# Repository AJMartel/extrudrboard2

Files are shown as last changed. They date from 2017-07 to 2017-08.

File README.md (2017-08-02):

# Extrudrboard2
Proposed revision of [Printrbot] [Extrudrboard] for
multi-color/multimaterial printing

Thing tracker at
https://cscott.github.io/thing-tracker/#/thing/737eb982-b77f-43e0-ae38-4fc30f3e3170

## Description

The latest revision of the [Printrboard] (REV F6) is mildly incompatible
with the original [Extrudrboard],
since the HOTEND A signal used by the Extrudrboard was disconnected
and used to provide an extruder fan output.

Also, multimaterial printing doesn't actually need all of the extra
hotend and thermistor inputs.

This repo contains a proposed "Extrudrboard2" which is compatible with
Printrboard REV F6 and provides up to four additional stepper outputs,
used for multimaterial bowden extruders.  The original Printrboard
extruder stepper is used for the direct drive just before the hotend,
and these additional Extrudrboard outputs are multiplexed and used for
the individual filament options.

As a bonus, I've thrown in a FAN2 output for owners of REV F5 and
earlier Printrboards, which adds an extruder fan output which works
identically to that on the REV F6 Printrboard.

The multiplexing scheme here is inspired by the "[Super Switch]" of
Prusa, and in fact basically the same [Marlin] code (`MK2_MULTIPLEXER`)
can be used.  One wrinkle is that the Printrboard extruder output
(we'll call it E0) wants to be a [Gear Head Extruder] with 127
steps/mm, while the individual bowden drivers (E1-E4, driven by the
Extrudrboard2) may be the lower cost 96 steps/mm [Alu Extruder]s --
or even the short-lived injection-molded plastic extruder.  So some
software cleverness is needed to allow multiplexing different
extruders with potentially different steps/mm rates.

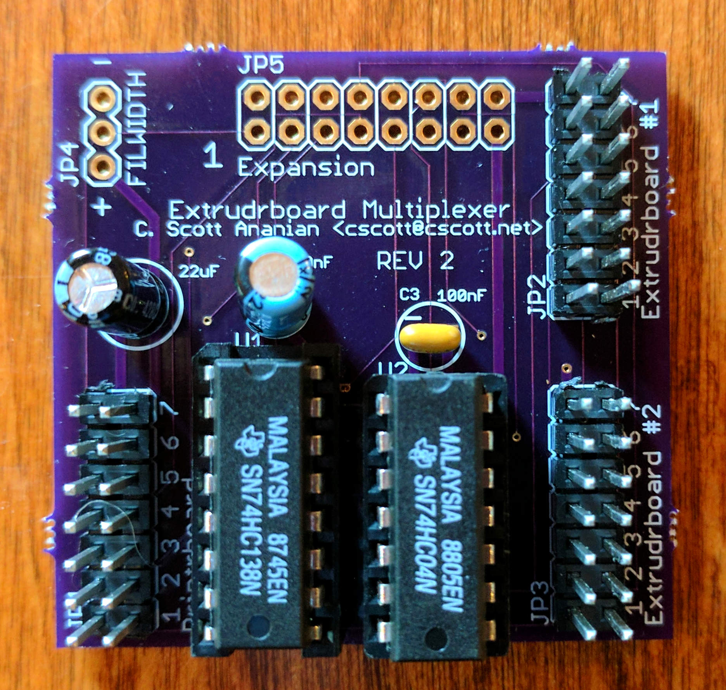
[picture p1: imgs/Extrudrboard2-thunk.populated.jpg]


There are two versions of the board here.  The [`Extrudrboard2-thunk.sch`]
files are an initial
prototype that allows you to connect two original Extrudrboards to the
Printrboard using the new multiplexing signal scheme.  It uses some
random logic ICs for the multiplexer that I just happened to have in
my toolbox.  There was a three-unit minimum order, so I've got a couple extra.  You
could also order this from [OSH Park] as shared project
[wLrvnUeh](https://oshpark.com/shared_projects/wLrvnUeh) -- warning,
boards are not yet tested!

If Printrbot decided to actually adopt this "project" as a "product",
they'd want something more like [`Extrudrboard2.sch`], which integrates the
four stepper drivers from the two old extrudrboards into a single new
board.  I actually reused as much as possible of the original
Extrudrboard schematic, components, and component packages, so this
should be highly compatible with whatever manufacturing process
Printrbot had for the original Extrudrboard.

<br clear="both" />

## Instructions

### Choose your build

If you have existing [Extrudrboard]s you wish to upgrade to the new
Extrudrboard2 functionality, use [`Extrudrboard2-thunk.sch`] with 1 or
2 original Extrudrboards connected.  If you are making new boards from
scratch, use [`Extrudrboard2.sch`].

### Assembling `Extrudrboard2-thunk`



Populating the PCB is straight-forward.  Three 7x2 0.1" male headers get
soldered in for "Printrboard", "Extrudrboard #1" and "Extrudrboard #2".
Add three bypass caps.  Values are somewhat flexible, but I used one 22uF
(primarily to decouple `FILWIDTH`) and two 0.1uF caps (to decouple the
logic ICs).  Solder in the 74HC138 and 74HC04; use DIP sockets if you like.
Note that the 74HC238 is actually a better fit here, but I just happened
to have a '138 in my toolbox so I added an inverter chip to make it work.
Likewise, you should feel free to use the LS or other variant of the logic
chips if you prefer: we're running on 5V and low speed, so any version
will do.

<br clear="both" />

### Wiring `Extrudrboard2-thunk`

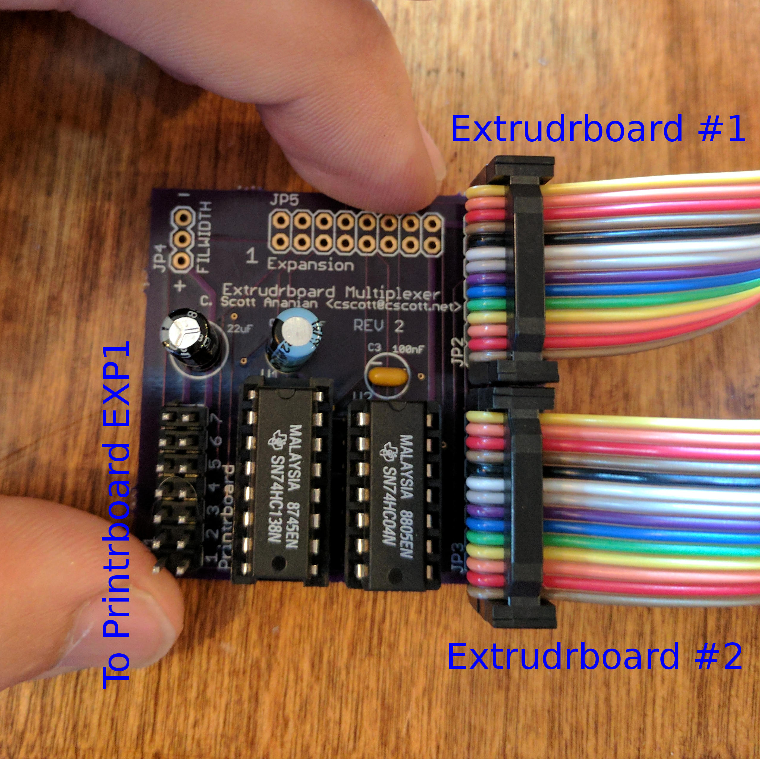
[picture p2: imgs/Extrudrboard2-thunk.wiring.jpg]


Use three 2x7 header cables to connect the Printrboard and two Extrudrboards
as indicated.  The tricky part is keeping pin 1 on the cables oriented
correctly, especially as neither the Printrboard nor the Extrudrboards clearly
mark pin 1.

<br clear="both" />
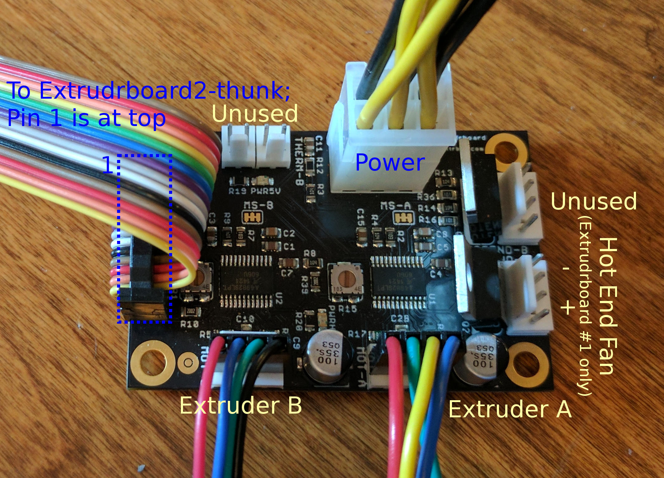
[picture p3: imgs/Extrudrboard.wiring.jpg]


You can connect a hotend fan to the HOTEND A output of Extrudrboard #1.
Pins 1 and 2 are shorted together, as are pins 3 and 4.  You probably
want to use a 1x2 female header on the center two pins.  I've marked
the polarity.

<br clear="both" />

### Additional features of `Extrudrboard2-thunk`

The `FILWIDTH` header is intended to support the Objects with Intelligence
[Filament Width Sensor](http://objectswithintelligence.weebly.com/store.html)
([thing:454584](https://www.thingiverse.com/thing:454584)), at the default
pin assignment used in upstream Marlin.  This is experimental: my
[multimaterial merge project](https://github.com/cscott/3d-multimaterial)
using the Extrudrboard2 doesn't have a place for this, and at the moment
I believe that minimizing distance between the merge and the gear head
drive is essential, so if I wanted to use it I'd likely have to significantly
re-engineer the filament width sensor to minimize the distance it would
add to the unsupported filament path.

The `EXPANSION` header brings all of the unused signals from both the
Printrboard EXP1 connector and the two Extrudrboard connectors into a
convenient place.  The 3 of the 4 HOTEND MOSFETs from the Extrudrboards
are unused (one is connected as an extruder fan output); it should be
convenient to use this header to wire them up to an unused signal from
EXP1 in order to drive some auxiliary load: extra lights, heaters, etc.

### Assembling `Extrudrboard2`

TBD...

### Wiring `Extrudrboard2`

TBD...

## Related

* [Forum discussion for this project](http://forum.monstercafe.net/topic5.html)
* [Multimaterial project](https://github.com/cscott/3d-multimaterial)
* [Repo for original Printrboard/Extruderboard](https://github.com/Printrbot/printrboard)

## License

These designs are released under the
[Creative Commons Attribution Share Alike 3.0] license, like the
original [Extrudrboard](https://github.com/Printrbot/printrboard#printrboard).

[Printrbot]: http://printrbot.com
[Printrboard]: http://reprap.org/wiki/Printrboard
[Extrudrboard]: http://reprap.org/wiki/Adding_more_extruders#RAMPS_using_ExtrudrBoard
[Marlin]: http://www.marlinfw.org/
[Super Switch]: https://github.com/prusa3d/Original-Prusa-i3/issues/29
[Gear Head Extruder]: https://printrbot.com/shop/gear-head-extruder-v2/
[Alu Extruder]: https://printrbot.com/shop/printrbot-alu-extruder-v2/
[`Extrudrboard2.sch`]: ./Extrudrboard2.sch.pdf
[`Extrudrboard2-thunk.sch`]: ./Extrudrboard2-thunk.sch.pdf
[OSH Park]: https://oshpark.com
[Creative Commons Attribution Share Alike 3.0]: https://spdx.org/licenses/CC-BY-SA-3.0.html

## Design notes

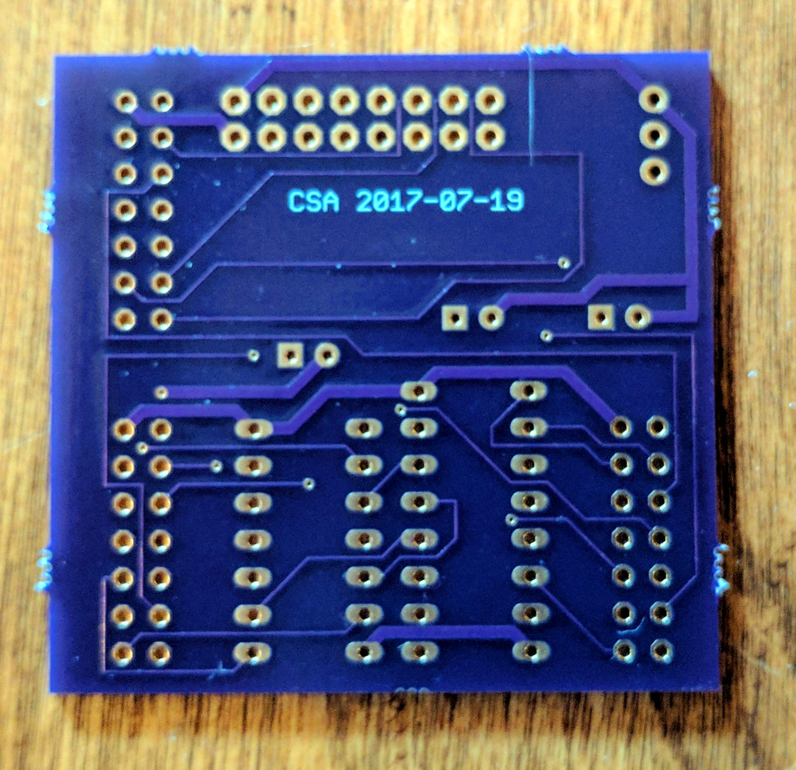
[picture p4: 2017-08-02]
imgs/Extrudrboard2-thunk.brd-back.jpg

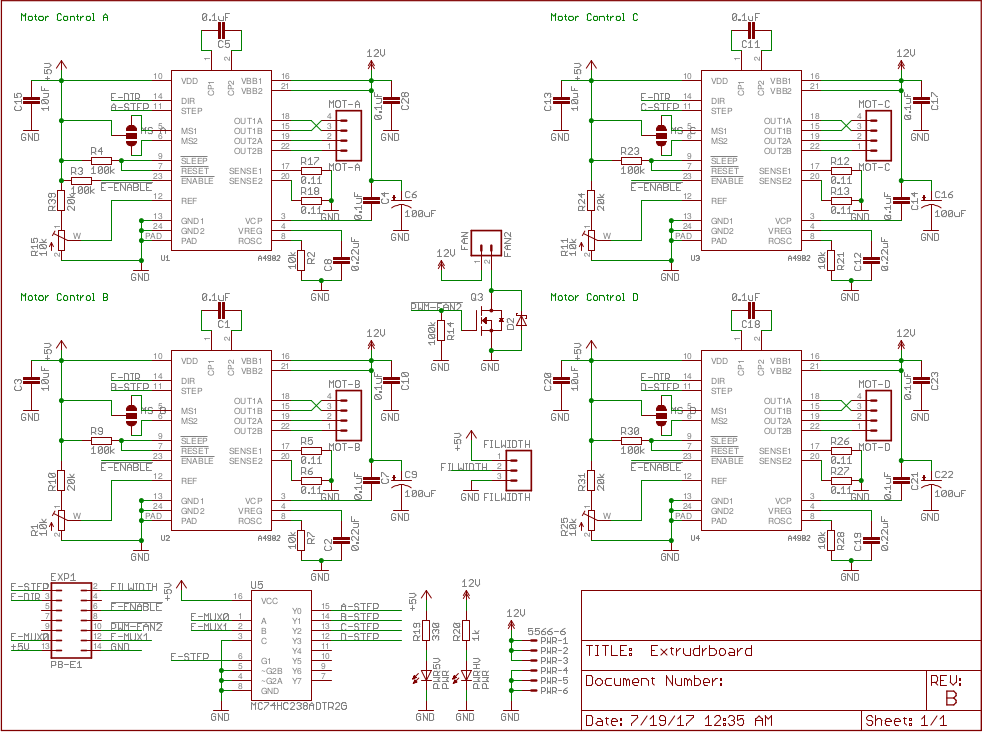
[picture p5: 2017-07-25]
imgs/Extrudrboard2.sch.png

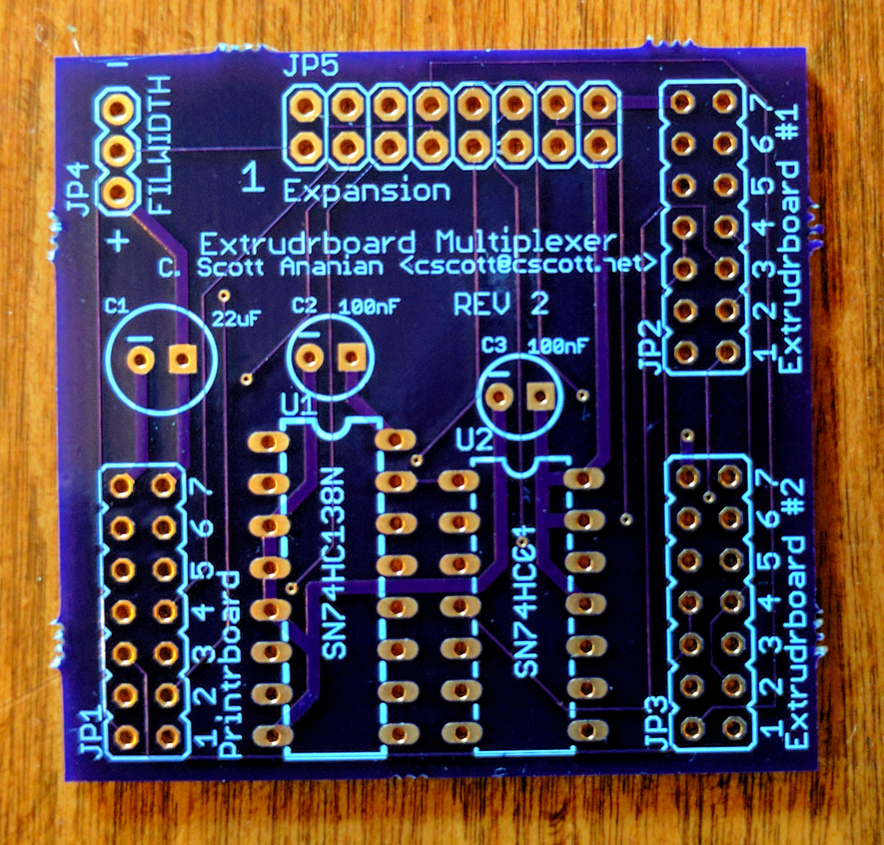
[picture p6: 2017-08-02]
imgs/Extrudrboard2-thunk.brd-front.jpg

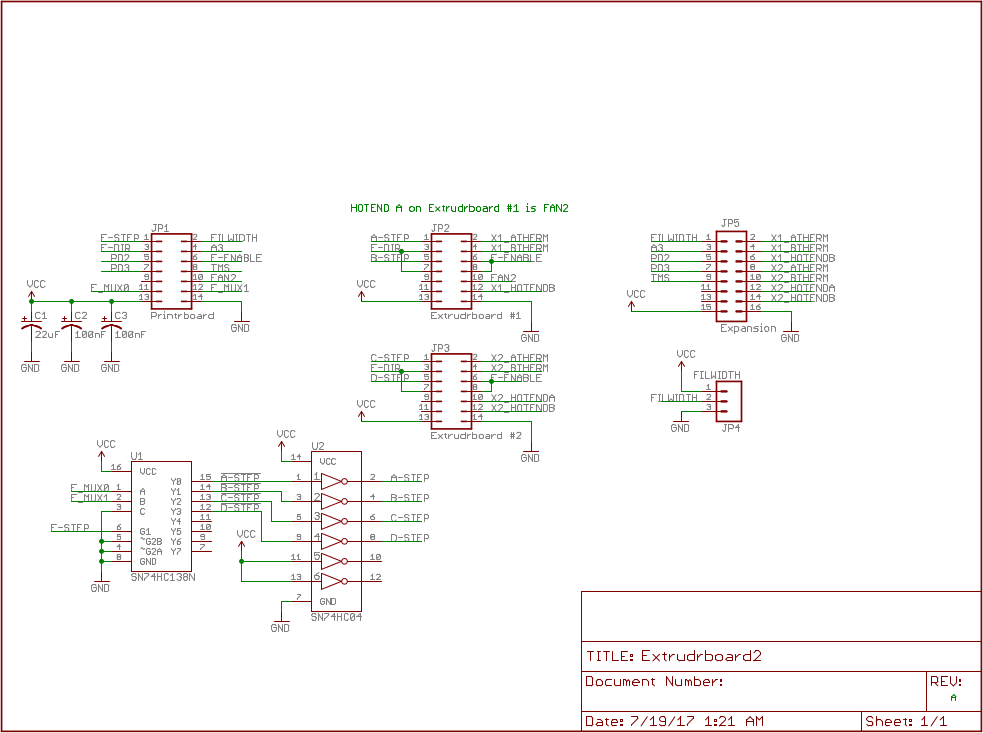
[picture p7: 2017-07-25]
imgs/Extrudrboard2-thunk.sch.png

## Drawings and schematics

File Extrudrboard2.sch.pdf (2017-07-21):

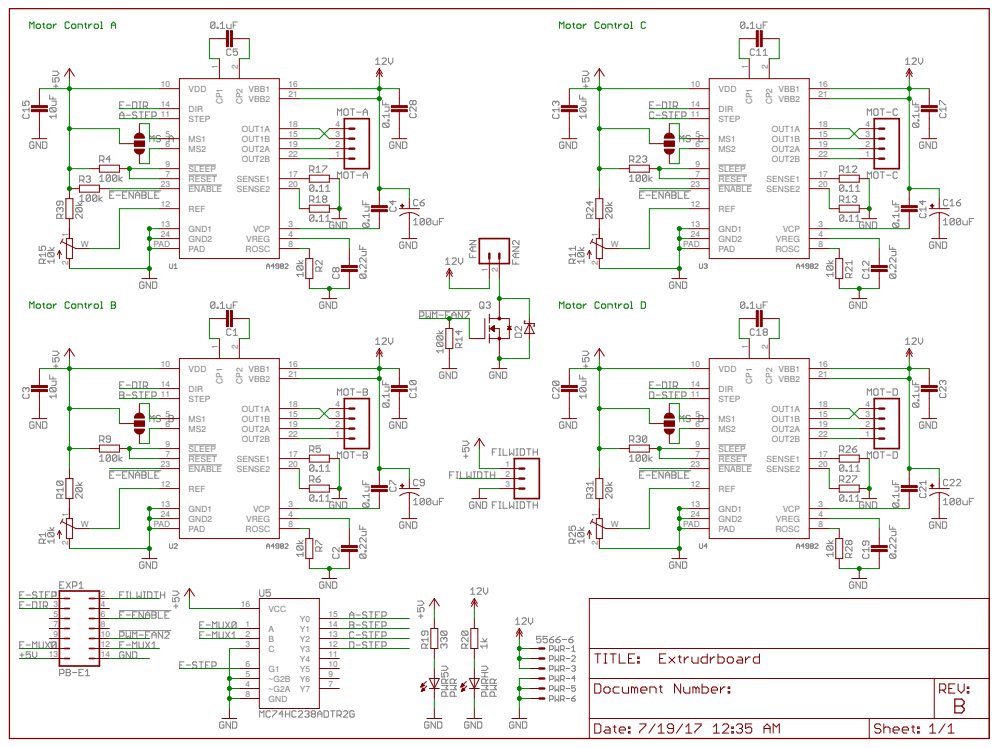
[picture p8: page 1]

2 1 W CP1 1 CP2 2 ROSC 8 VBB2 21 VDD 10 VBB1 16 OUT1A 18 OUT1B 15 OUT2A 19 OUT2B 22 SENSE1 17 SENSE2 20 VREG 4 GND1 13 REF 12 ENABLE 23 MS1 5 RESET 7 STEP 11 DIR 14 VCP 3 SLEEP 9 GND2 24 PAD PAD MS2 6 1234 2 1 W CP1 1 CP2 2 ROSC 8 VBB2 21 VDD 10 VBB1 16 OUT1A 18 OUT1B 15 OUT2A 19 OUT2B 22 SENSE1 17 SENSE2 20 VREG 4 GND1 13 REF 12 ENABLE 23 MS1 5 RESET 7 STEP 11 DIR 14 VCP 3 SLEEP 9 GND2 24 PAD PAD MS2 6 1234 1 2 3 4 5 6 7 8 9 10 11 12 13 14 2 1 W CP1 1 CP2 2 ROSC 8 VBB2 21 VDD 10 VBB1 16 OUT1A 18 OUT1B 15 OUT2A 19 OUT2B 22 SENSE1 17 SENSE2 20 VREG 4 GND1 13 REF 12 ENABLE 23 MS1 5 RESET 7 STEP 11 DIR 14 VCP 3 SLEEP 9 GND2 24 PAD PAD MS2 6 1234 2 1 W CP1 1 CP2 2 ROSC 8 VBB2 21 VDD 10 VBB1 16 OUT1A 18 OUT1B 15 OUT2A 19 OUT2B 22 SENSE1 17 SENSE2 20 VREG 4 GND1 13 REF 12 ENABLE 23 MS1 5 RESET 7 STEP 11 DIR 14 VCP 3 SLEEP 9 GND2 24 PAD PAD MS2 6 1234 VCC 16 A 1 B 2 C 3 G1 6 ~G2B 5 ~G2A 4 GND 8 Y7 7 Y6 9 Y5 10 Y4 11 Y3 12 Y2 13 Y1 14 Y0 15 12 123

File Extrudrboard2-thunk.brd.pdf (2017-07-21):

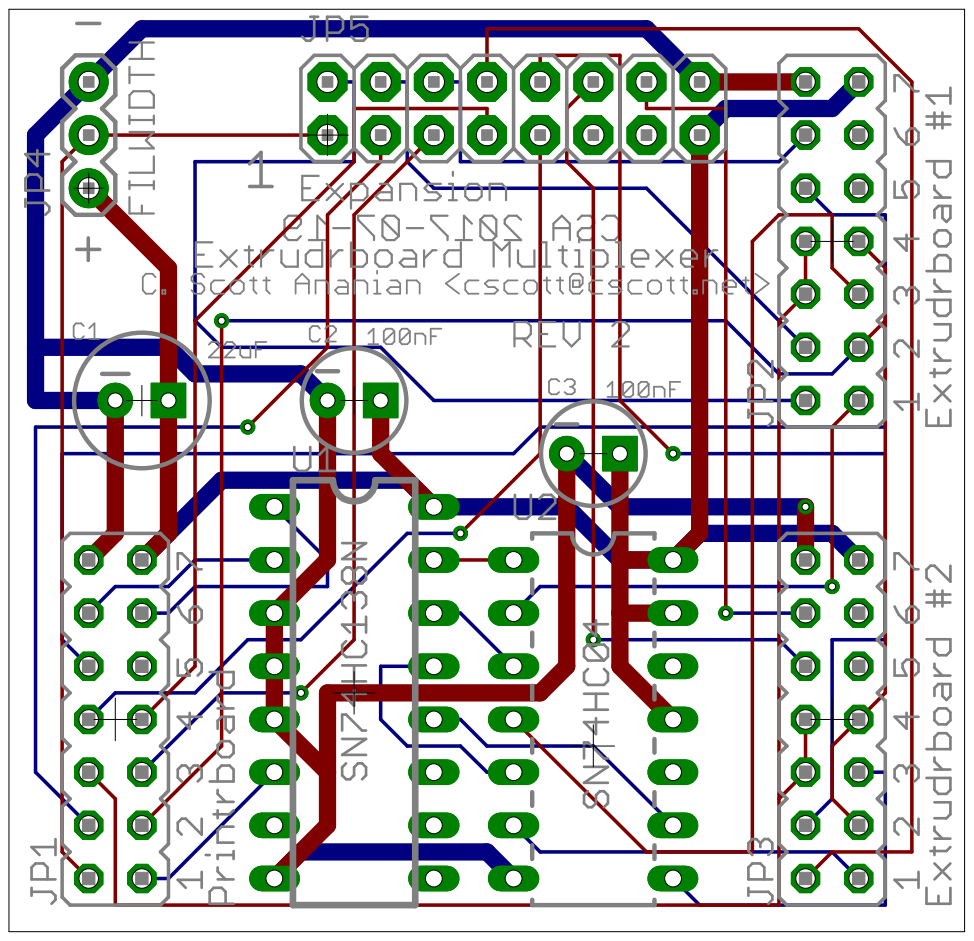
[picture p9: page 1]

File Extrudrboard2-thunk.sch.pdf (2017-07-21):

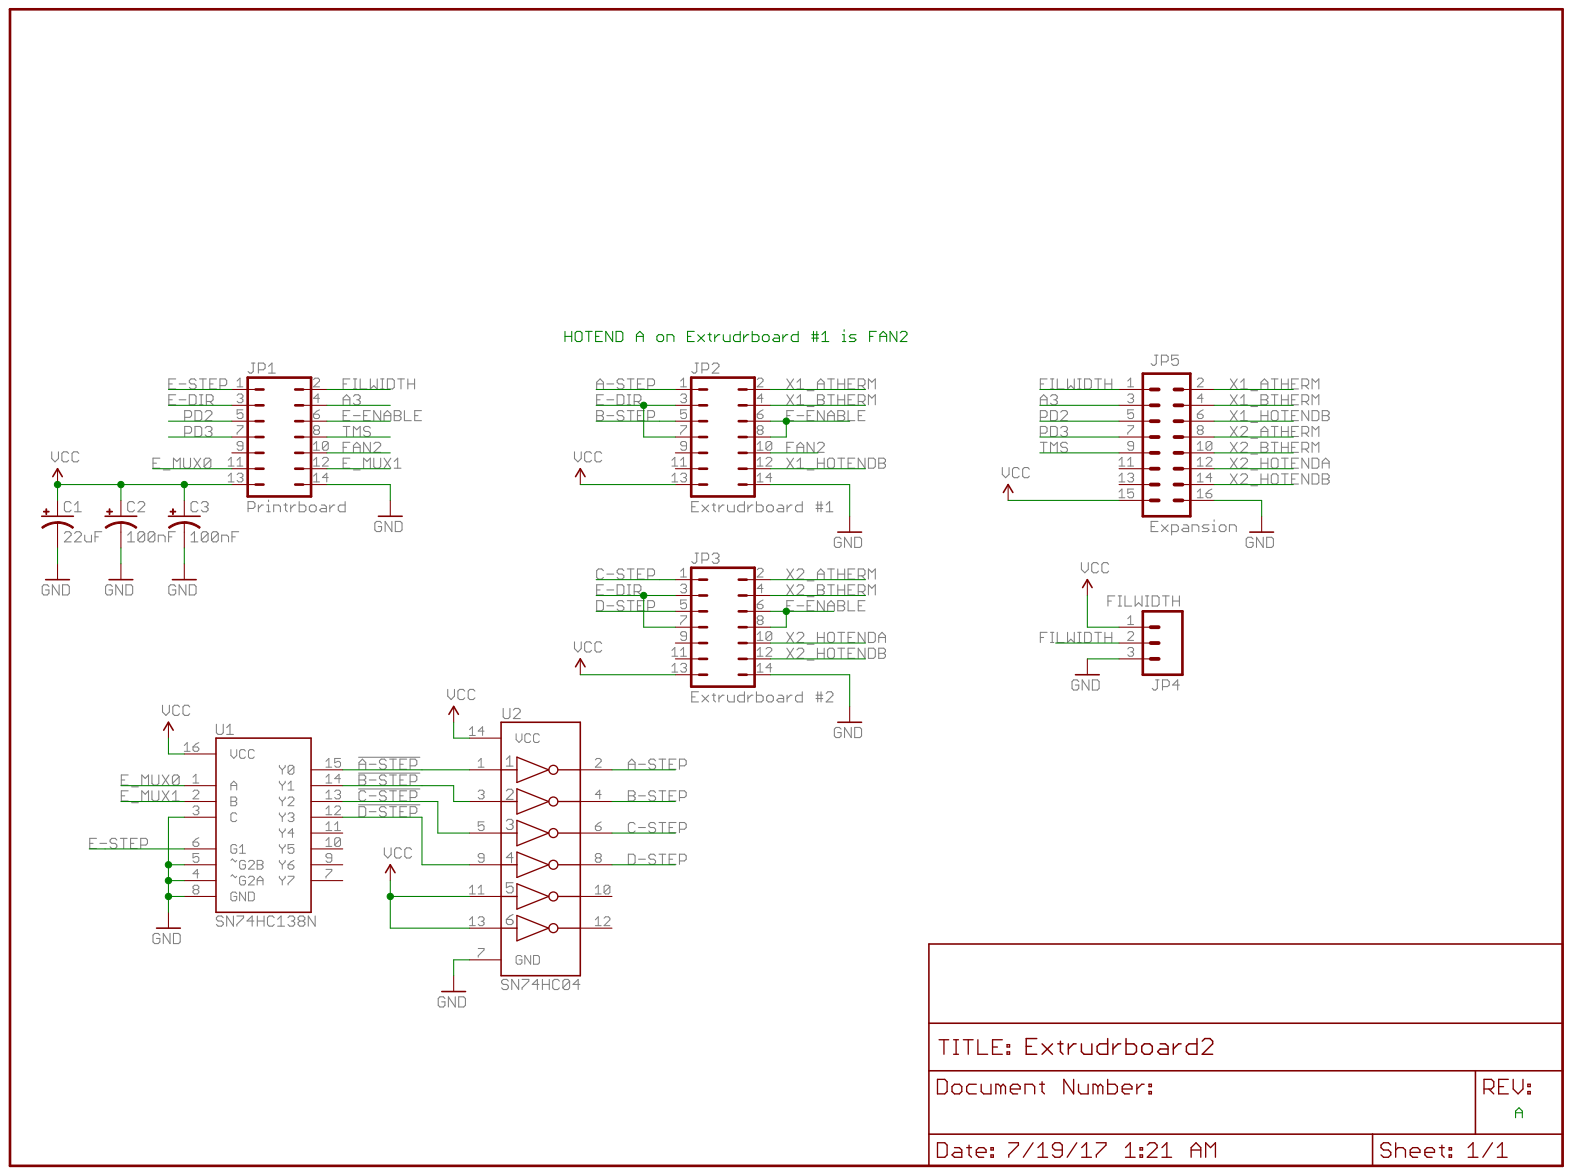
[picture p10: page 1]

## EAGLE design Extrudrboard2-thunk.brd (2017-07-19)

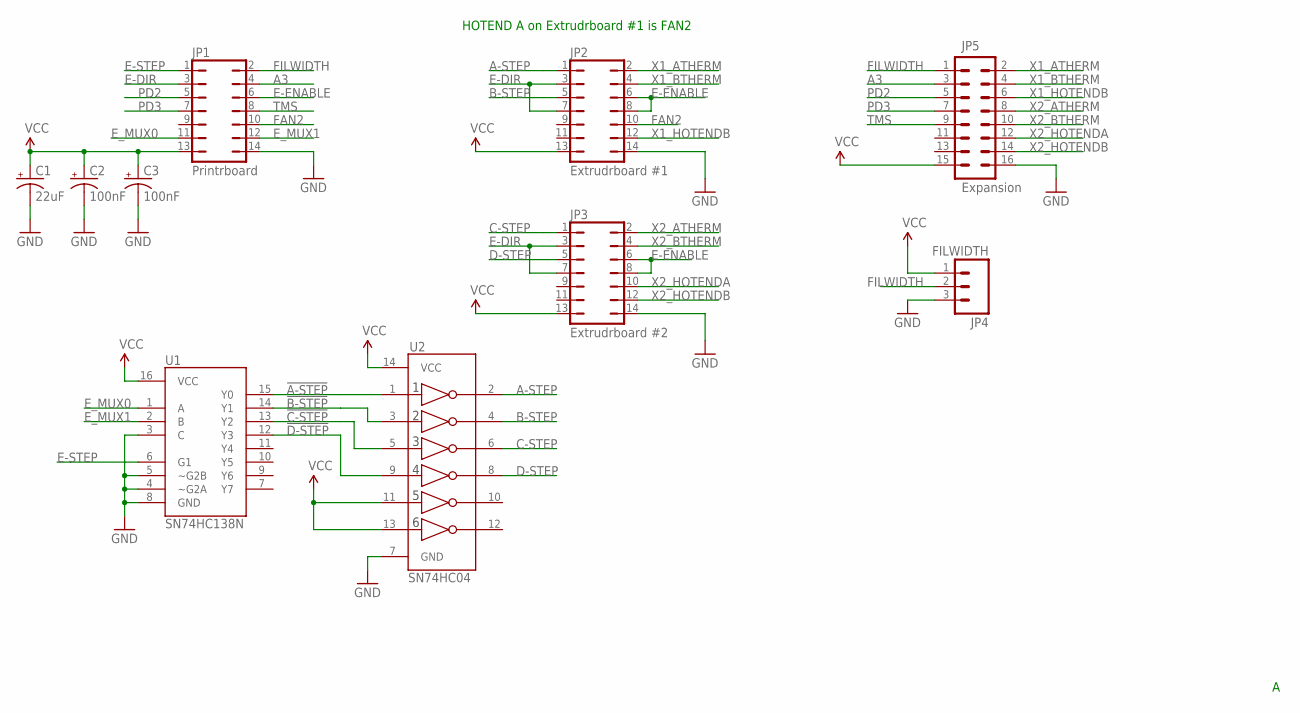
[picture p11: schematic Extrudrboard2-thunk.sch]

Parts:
C1: 22uF; CPOL-RADIAL-100UF-25V
C2, C3: 100nF; CPOL-RADIAL-10UF-25V
JP1: Printrboard; JP7Q
JP2: Extrudrboard #1; JP7Q
JP3: Extrudrboard #2; JP7Q
JP4: FILWIDTH; 1X03
JP5: Expansion; 2X8
U1: SN74HC138N; DIL16
U2: SN74HC04; DIL14

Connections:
!A-STEP: U1.15 (Y0), U2.1 (1A)
!B-STEP: U1.14 (Y1), U2.3 (2A)
!C-STEP: U1.13 (Y2), U2.5 (3A)
!D-STEP: U1.12 (Y3), U2.9 (4A)
A3: JP1.4, JP5.3
A-STEP: JP2.1, U2.2 (1Y)
B-STEP: JP2.5, U2.4 (2Y)
C-STEP: JP3.1, U2.6 (3Y)
D-STEP: JP3.5, U2.8 (4Y)
E-DIR: JP1.3, JP2.3, JP2.7, JP3.3, JP3.7
E-ENABLE: JP1.6, JP2.6, JP2.8, JP3.6, JP3.8
E-STEP: JP1.1, U1.6 (G1)
E_MUX0: JP1.11, U1.1 (A)
E_MUX1: JP1.12, U1.2 (B)
FAN2: JP1.10, JP2.10
FILWIDTH: JP1.2, JP4.2, JP5.1
GND: C1.2 (-), C2.2 (-), C3.2 (-), JP1.14, JP2.14, JP3.14, JP4.3, JP5.16, U1.3 (C), U1.4 (~G2A), U1.5 (~G2B), U1.8 (GND), U2.7 (GND)
PD2: JP1.5, JP5.5
PD3: JP1.7, JP5.7
TMS: JP1.8, JP5.9
VCC: C1.1 (+), C2.1 (+), C3.1 (+), JP1.13, JP2.13, JP3.13, JP4.1, JP5.15, U1.16 (VCC), U2.11 (5A), U2.13 (6A), U2.14 (VCC)
X1_ATHERM: JP2.2, JP5.2
X1_BTHERM: JP2.4, JP5.4
X1_HOTENDB: JP2.12, JP5.6
X2_ATHERM: JP3.2, JP5.8
X2_BTHERM: JP3.4, JP5.10
X2_HOTENDA: JP3.10, JP5.12
X2_HOTENDB: JP3.12, JP5.14

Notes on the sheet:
HOTEND A on Extrudrboard #1 is FAN2

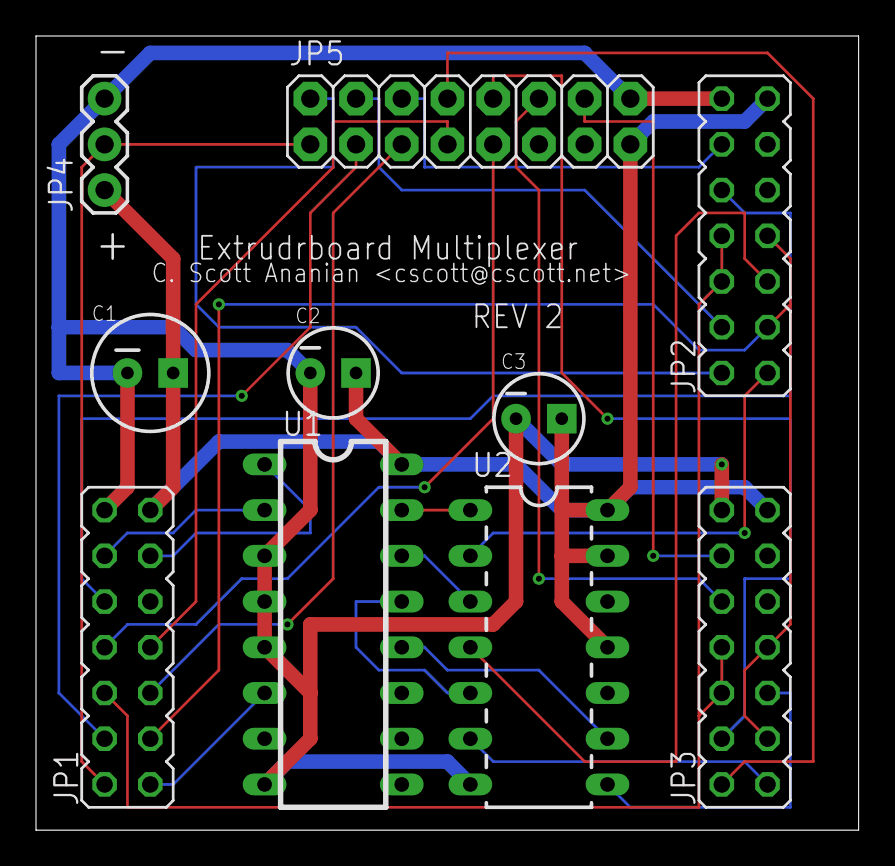
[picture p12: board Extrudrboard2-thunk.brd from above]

Board: 2 copper layers, 45.7 x 44.1 mm, 10 parts (0 on the bottom side), 28 nets.

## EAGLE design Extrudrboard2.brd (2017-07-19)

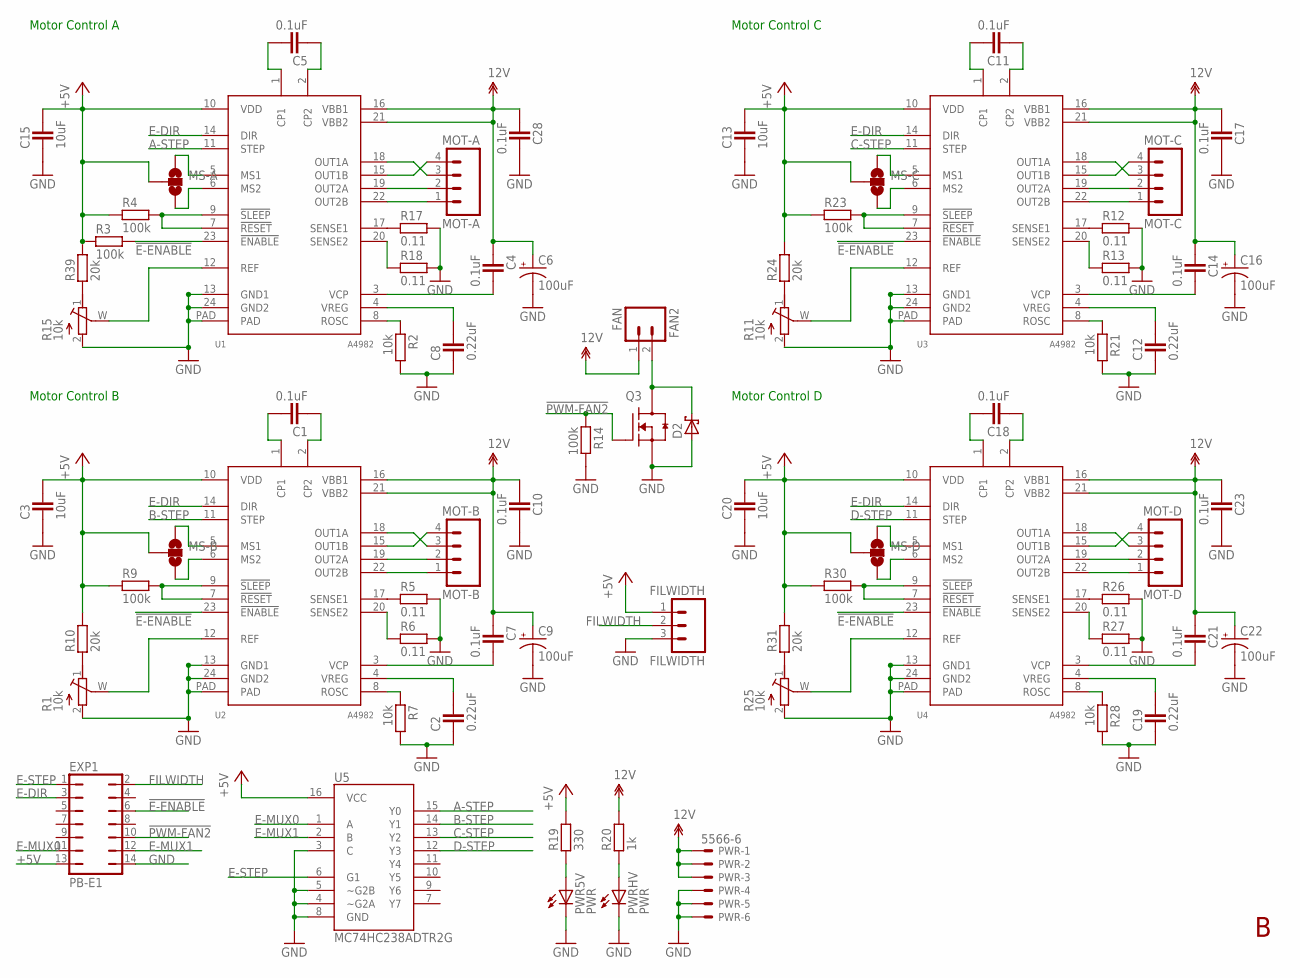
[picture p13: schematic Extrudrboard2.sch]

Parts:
C1, C4, C5, C7, C10, C11, C14, C17, C18, C21, C23, C28: 0.1uF; CAPC2012X145AN
C2, C8, C12, C19: 0.22uF; CAPC2012X145AN
C3, C13, C15, C20: 10uF; CAPC2012X145AN
C6, C9, C16, C22: 100uF; PANASONIC_D
D2: SCH-DIODESMA; SMA
EXP1: PB-E1; JP7Q
FAN2: FAN; 1X02
FILWIDTH: FILWIDTH; 1X03
MOT-A: MOT-A; MOLEX-1X4
MOT-B: MOT-B; MOLEX-1X4
MOT-C: MOT-C; MOLEX-1X4
MOT-D: MOT-D; MOLEX-1X4
MS-A: SOLDERJUMPER_2WAYCONNECTED; SJ_3_CONNECTED
MS-B: SOLDERJUMPER_2WAYCONNECTED; SJ_3_CONNECTED
MS-C: SOLDERJUMPER_2WAYCONNECTED; SJ_3_CONNECTED
MS-D: SOLDERJUMPER_2WAYCONNECTED; SJ_3_CONNECTED
PWR: 5566-6
PWR5V: PWR; CHIP-LED0805
PWRHV: PWR; CHIP-LED0805
Q3: RFP30N06LE; SOT95P280X135-3N
R1, R11, R15, R25: 10k; RTRIM-ST4ETB
R2, R7, R21, R28: 10k; RESC2012X70N
R3, R4, R9, R14, R23, R30: 100k; RESC2012X70N
R5, R6, R12, R13, R17, R18, R26, R27: 0.11; RESC2012X70N
R10, R24, R31, R39: 20k; RESC2012X70N
R19: 330; RESC2012X70N
R20: 1k; RESC2012X70N
U1, U2, U3, U4: A4982; TSSOP-24
U5: MC74HC238ADTR2G; TSSOP16

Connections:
12V: C4.1, C6.+, C7.1, C9.+, C10.1, C14.1, C16.+, C17.1, C21.1, C22.+, C23.1, C28.1, FAN2.1, PWR.1, PWR.2, PWR.3, R20.2, U1.16 (VBB1), U1.21 (VBB2), U2.16 (VBB1), U2.21 (VBB2), U3.16 (VBB1), U3.21 (VBB2), U4.16 (VBB1), U4.21 (VBB2)
!E-ENABLE: EXP1.6, R3.2, U1.23 (!ENABLE), U2.23 (!ENABLE), U3.23 (!ENABLE), U4.23 (!ENABLE)
!PWM-FAN2: EXP1.10, Q3.1 (G), R14.1
+5V: C3.2, C13.2, C15.2, C20.2, EXP1.13, FILWIDTH.1, MS-A.2, MS-B.2, MS-C.2, MS-D.2, R3.1, R4.1, R9.1, R10.2, R19.2, R23.1, R24.2, R30.1, R31.2, R39.2, U1.10 (VDD), U2.10 (VDD), U3.10 (VDD), U4.10 (VDD), U5.16 (VCC)
A-STEP: U1.11 (STEP), U5.15 (Y0)
B-STEP: U2.11 (STEP), U5.14 (Y1)
C-STEP: U3.11 (STEP), U5.13 (Y2)
D-STEP: U4.11 (STEP), U5.12 (Y3)
E-DIR: EXP1.3, U1.14 (DIR), U2.14 (DIR), U3.14 (DIR), U4.14 (DIR)
E-MUX0: EXP1.11, U5.1 (A)
E-MUX1: EXP1.12, U5.2 (B)
E-STEP: EXP1.1, U5.6 (G1)
FILWIDTH: EXP1.2, FILWIDTH.2
GND: C2.1, C3.1, C6.-, C8.1, C9.-, C10.2, C12.1, C13.1, C15.1, C16.-, C17.2, C19.1, C20.1, C22.-, C23.2, C28.2, D2.A, EXP1.14, FILWIDTH.3, PWR.4, PWR.5, PWR.6, PWR5V.C, PWRHV.C, Q3.2 (S), R1.2 (E), R2.2, R5.2, R6.2, R7.2, R11.2 (E), R12.2, R13.2, R14.2, R15.2 (E), R17.2, R18.2, R21.2, R25.2 (E), R26.2, R27.2, R28.2, U1.13 (GND1), U1.24 (GND2), U1.PAD, U2.13 (GND1), U2.24 (GND2), U2.PAD, U3.13 (GND1), U3.24 (GND2), U3.PAD, U4.13 (GND1), U4.24 (GND2), U4.PAD, U5.3 (C), U5.4 (~G2A), U5.5 (~G2B), U5.8 (GND)
unnamed: C1.2, U2.1 (CP1)
unnamed: C1.1, U2.2 (CP2)
unnamed: R5.1, U2.17 (SENSE1)
unnamed: R6.1, U2.20 (SENSE2)
unnamed: R1.W (S), U2.12 (REF)
unnamed: R7.1, U2.8 (ROSC)
unnamed: C2.2, U2.4 (VREG)
unnamed: R9.2, U2.7 (!RESET), U2.9 (!SLEEP)
unnamed: C7.2, U2.3 (VCP)
unnamed: MOT-A.3, U1.18 (OUT1A)
unnamed: C5.2, U1.1 (CP1)
unnamed: C5.1, U1.2 (CP2)
unnamed: R2.1, U1.8 (ROSC)
unnamed: R17.1, U1.17 (SENSE1)
unnamed: R18.1, U1.20 (SENSE2)
unnamed: C4.2, U1.3 (VCP)
unnamed: MOT-A.4, U1.15 (OUT1B)
unnamed: R15.W (S), U1.12 (REF)
unnamed: C8.2, U1.4 (VREG)
unnamed: MOT-A.2, U1.19 (OUT2A)
unnamed: R4.2, U1.7 (!RESET), U1.9 (!SLEEP)
unnamed: MS-B.1, U2.5 (MS1)
unnamed: MOT-A.1, U1.22 (OUT2B)
unnamed: MS-B.3, U2.6 (MS2)
unnamed: MOT-B.3, U2.18 (OUT1A)
unnamed: MOT-B.4, U2.15 (OUT1B)
unnamed: MS-A.1, U1.5 (MS1)
unnamed: MS-A.3, U1.6 (MS2)
unnamed: MOT-B.2, U2.19 (OUT2A)
unnamed: MOT-B.1, U2.22 (OUT2B)
unnamed: R1.1 (A), R10.1
unnamed: PWR5V.A, R19.1
unnamed: PWRHV.A, R20.1
unnamed: C11.2, U3.1 (CP1)
unnamed: C11.1, U3.2 (CP2)
unnamed: R12.1, U3.17 (SENSE1)
unnamed: R13.1, U3.20 (SENSE2)
unnamed: R11.W (S), U3.12 (REF)
unnamed: R21.1, U3.8 (ROSC)
unnamed: C12.2, U3.4 (VREG)
unnamed: R23.2, U3.7 (!RESET), U3.9 (!SLEEP)
unnamed: C14.2, U3.3 (VCP)
unnamed: MS-C.1, U3.5 (MS1)
unnamed: MS-C.3, U3.6 (MS2)
unnamed: MOT-C.3, U3.18 (OUT1A)
unnamed: MOT-C.4, U3.15 (OUT1B)
unnamed: MOT-C.2, U3.19 (OUT2A)
unnamed: MOT-C.1, U3.22 (OUT2B)
unnamed: R11.1 (A), R24.1
unnamed: C18.2, U4.1 (CP1)
unnamed: C18.1, U4.2 (CP2)
unnamed: R26.1, U4.17 (SENSE1)
unnamed: R27.1, U4.20 (SENSE2)
unnamed: R25.W (S), U4.12 (REF)
unnamed: R28.1, U4.8 (ROSC)
unnamed: C19.2, U4.4 (VREG)
unnamed: R30.2, U4.7 (!RESET), U4.9 (!SLEEP)
unnamed: C21.2, U4.3 (VCP)
unnamed: MS-D.1, U4.5 (MS1)
unnamed: MS-D.3, U4.6 (MS2)
unnamed: MOT-D.3, U4.18 (OUT1A)
unnamed: MOT-D.4, U4.15 (OUT1B)
unnamed: MOT-D.2, U4.19 (OUT2A)
unnamed: MOT-D.1, U4.22 (OUT2B)
unnamed: R25.1 (A), R31.1
unnamed: D2.C, FAN2.2, Q3.3 (D)
unnamed: R15.1 (A), R39.1

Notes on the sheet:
Motor Control A
Motor Control B
Motor Control C
Motor Control D

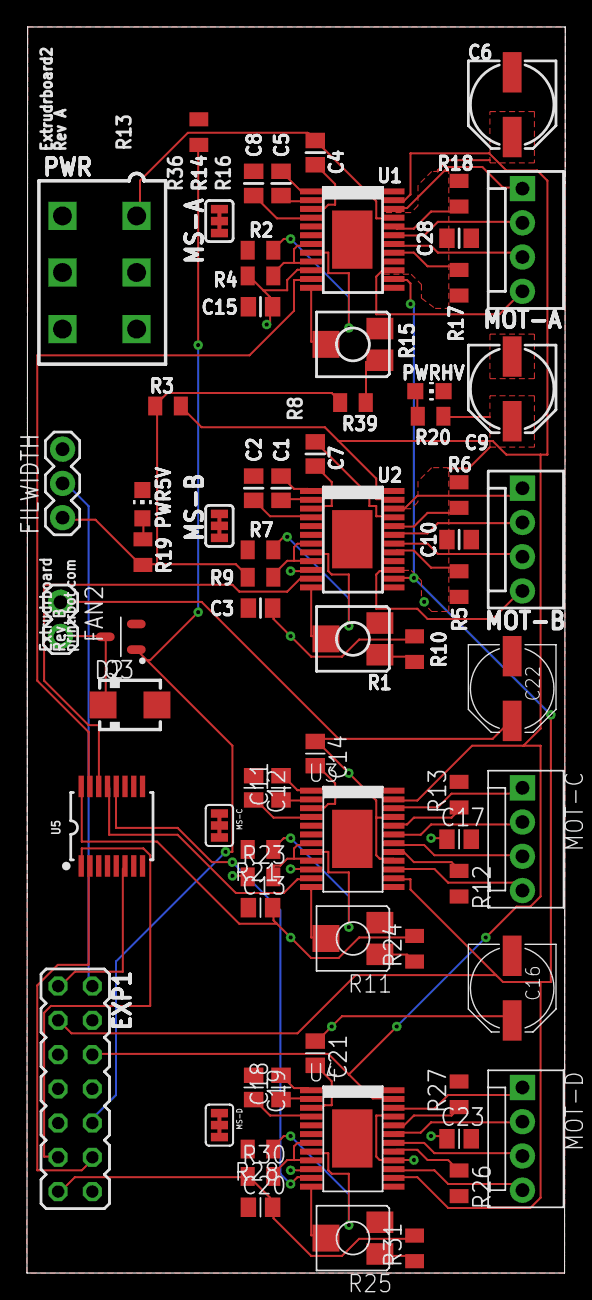
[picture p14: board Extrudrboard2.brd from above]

Board: 4 copper layers, 39.9 x 92.4 mm, 73 parts (0 on the bottom side), 81 nets.

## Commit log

2017-07-19 Initial board submission to OSH park. Multiplex the ENABLE lines.
    [Extrudrboard.brd, Extrudrboard.sch, Extrudrboard2.brd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]
2017-07-19 Multiplex STEP instead of ENABLE.
    [Extrudrboard2.brd, Extrudrboard2.sch]
2017-07-21 Add PDFs of schematics for better browsability.
2017-07-25 Rename Extrudrboard to Extrudrboard2 for clarity.
    [Extrudrboard.brd, Extrudrboard.sch, Extrudrboard2-thunk.brd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]
2017-08-02 Add photos of assembled Extrudrboard2-thunk; describe assembly and wiring.

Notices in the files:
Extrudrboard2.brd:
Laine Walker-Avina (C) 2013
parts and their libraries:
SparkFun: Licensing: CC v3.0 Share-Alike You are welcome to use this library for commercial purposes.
